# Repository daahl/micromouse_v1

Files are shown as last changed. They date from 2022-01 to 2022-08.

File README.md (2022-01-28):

# Micromouse_v1

This project aims to develop a [micromouse](https://www.youtube.com/results?search_query=micromouse) using a DOIT ESP32 dev module. The robot is powered by two 18620 batteries in series, and two micro metal motors fitted with encoders. The mapping is done using three VL53L0X TOF sensors.

**Currently a work in progress.**

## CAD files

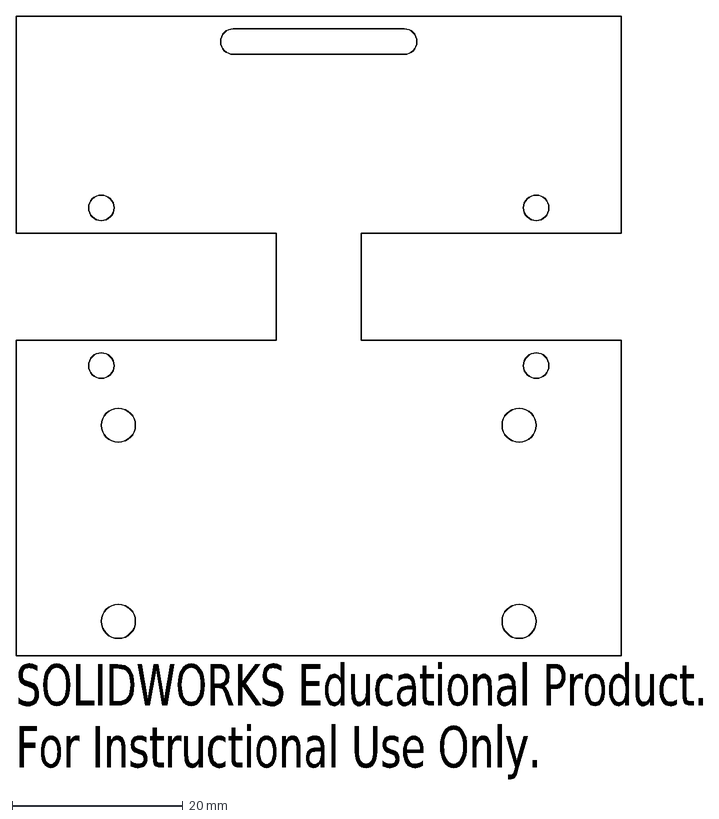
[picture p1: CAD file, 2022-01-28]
kicad_v2/PCB.dxf
SOLIDWORKS Educational Product.
For Instructional Use Only.

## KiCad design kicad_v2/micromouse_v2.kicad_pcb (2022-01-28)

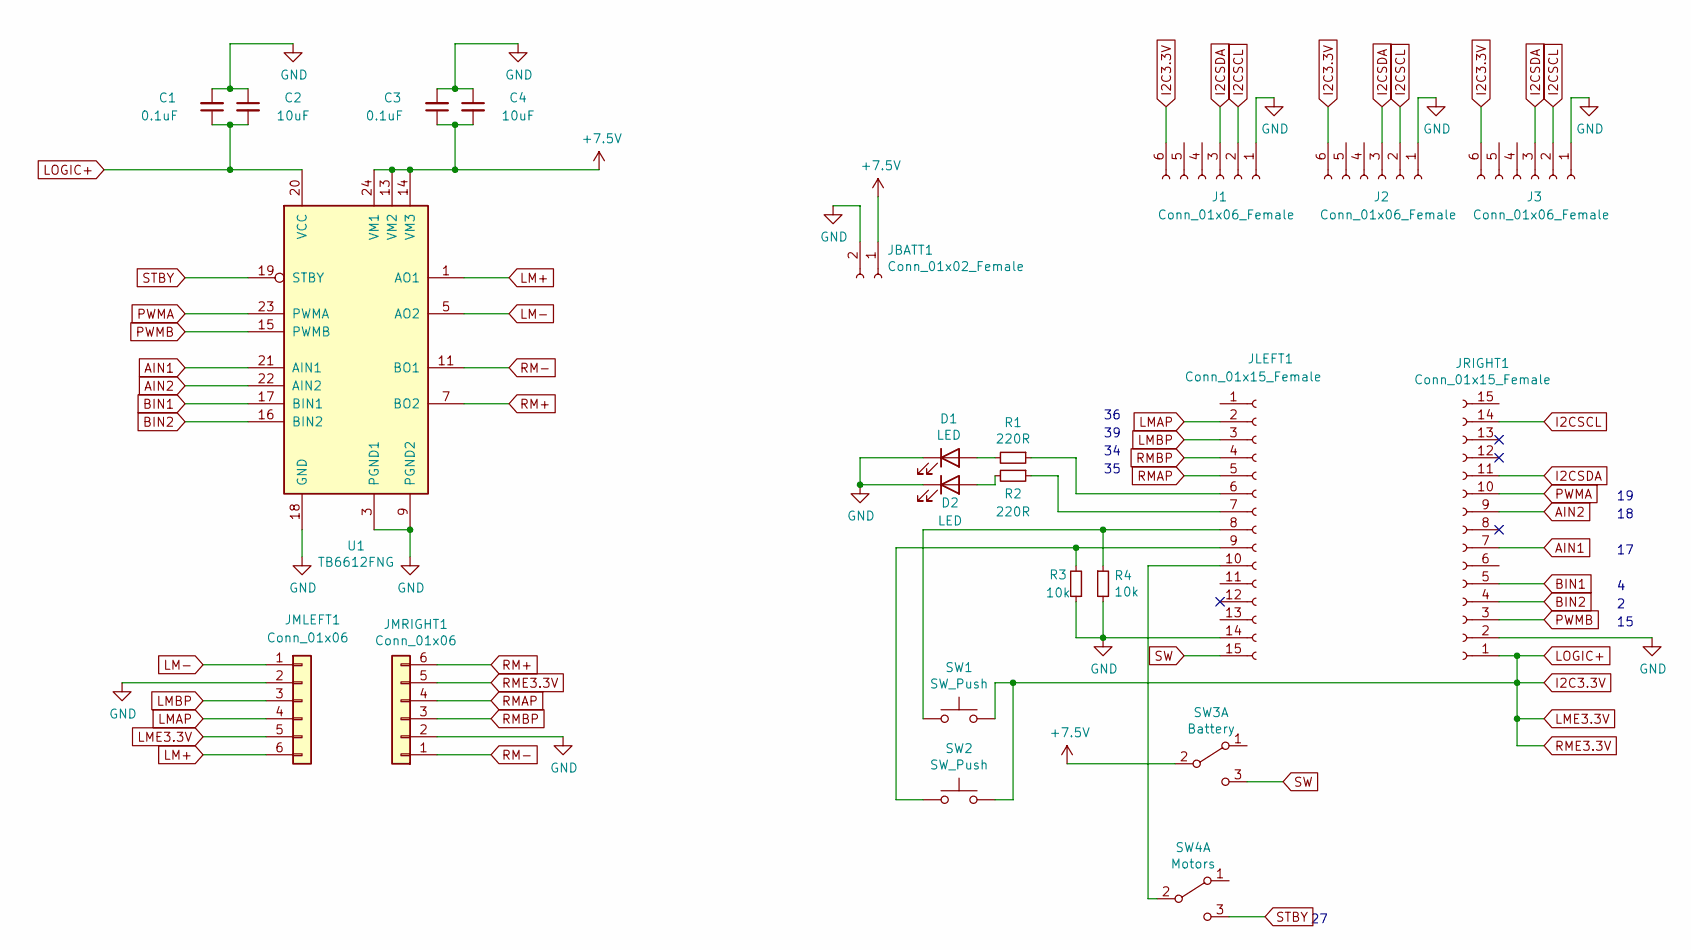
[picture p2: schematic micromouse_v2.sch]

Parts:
C1, C3: 0.1uF; C_0603_1608Metric_Pad1.08x0.95mm_HandSolder
C2, C4: 10uF; C_0603_1608Metric_Pad1.08x0.95mm_HandSolder
D1, D2: LED; LED_0603_1608Metric_Pad1.05x0.95mm_HandSolder
J1, J2, J3: Conn_01x06_Female; PinSocket_1x06_P2.54mm_Vertical
JBATT1: Conn_01x02_Female; JST_EH_B2B-EH-A_1x02_P2.50mm_Vertical
JLEFT1: Conn_01x15_Female; PinSocket_1x15_P2.54mm_Vertical
JMLEFT1: Conn_01x06; JST_EH_B6B-EH-A_1x06_P2.50mm_Vertical
JMRIGHT1: Conn_01x06; JST_EH_B6B-EH-A_1x06_P2.50mm_Vertical
JRIGHT1: Conn_01x15_Female; PinSocket_1x15_P2.54mm_Vertical
R1, R2: 220R; R_0603_1608Metric_Pad0.98x0.95mm_HandSolder
R3, R4: 10k; R_0603_1608Metric_Pad0.98x0.95mm_HandSolder
SW1, SW2: SW_Push; SW_SPST_Omron_B3FS-100xP
SW3: Battery; SW_CuK_OS102011MA1QN1_SPDT_Angled
SW4: Motors; SW_CuK_OS102011MA1QN1_SPDT_Angled
U1: TB6612FNG; SSOP-24_5.3x8.2mm_P0.65mm

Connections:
+7.5V: C3.1, C4.2, JBATT1.1, SW3.2 (B), U1.13 (VM2), U1.14 (VM3), U1.24 (VM1)
AIN1: JRIGHT1.7, U1.21 (AIN1)
AIN2: JRIGHT1.9, U1.22 (AIN2)
BIN1: JRIGHT1.5, U1.17 (BIN1)
BIN2: JRIGHT1.4, U1.16 (BIN2)
GND: C1.2, C2.1, C3.2, C4.1, D1.1 (K), D2.1 (K), J1.1, J2.1, J3.1, JBATT1.2, JLEFT1.14, JMLEFT1.2, JMRIGHT1.2, JRIGHT1.2, R3.1, R4.2, U1.3 (PGND1), U1.4 (PGND1), U1.9 (PGND2), U1.10 (PGND2), U1.18 (GND)
I2C3.3V: C1.1, C2.2, J1.6, J2.6, J3.6, JMLEFT1.5, JMRIGHT1.5, JRIGHT1.1, SW1.2, SW2.2, U1.20 (VCC)
I2CSCL: J1.2, J2.2, J3.2, JRIGHT1.14
I2CSDA: J1.3, J2.3, J3.3, JRIGHT1.11
LM+: JMLEFT1.6, U1.1 (AO1), U1.2 (AO1)
LM-: JMLEFT1.1, U1.5 (AO2), U1.6 (AO2)
LMAP: JLEFT1.2, JMLEFT1.4
LMBP: JLEFT1.3, JMLEFT1.3
unnamed: D1.2 (A), R1.2
unnamed: D2.2 (A), R2.2
unnamed: JLEFT1.6, R1.1
unnamed: JLEFT1.7, R2.1
unnamed: JLEFT1.8, R4.1, SW1.1
unnamed: JLEFT1.9, R3.2, SW2.1
unnamed: JLEFT1.10, SW4.2 (B)
PWMA: JRIGHT1.10, U1.23 (PWMA)
PWMB: JRIGHT1.3, U1.15 (PWMB)
RM+: JMRIGHT1.6, U1.7 (BO2), U1.8 (BO2)
RM-: JMRIGHT1.1, U1.11 (BO1), U1.12 (BO1)
RMAP: JLEFT1.5, JMRIGHT1.4
RMBP: JLEFT1.4, JMRIGHT1.3
STBY: SW4.3 (C), U1.19 (STBY)
SW: JLEFT1.15, SW3.3 (C)

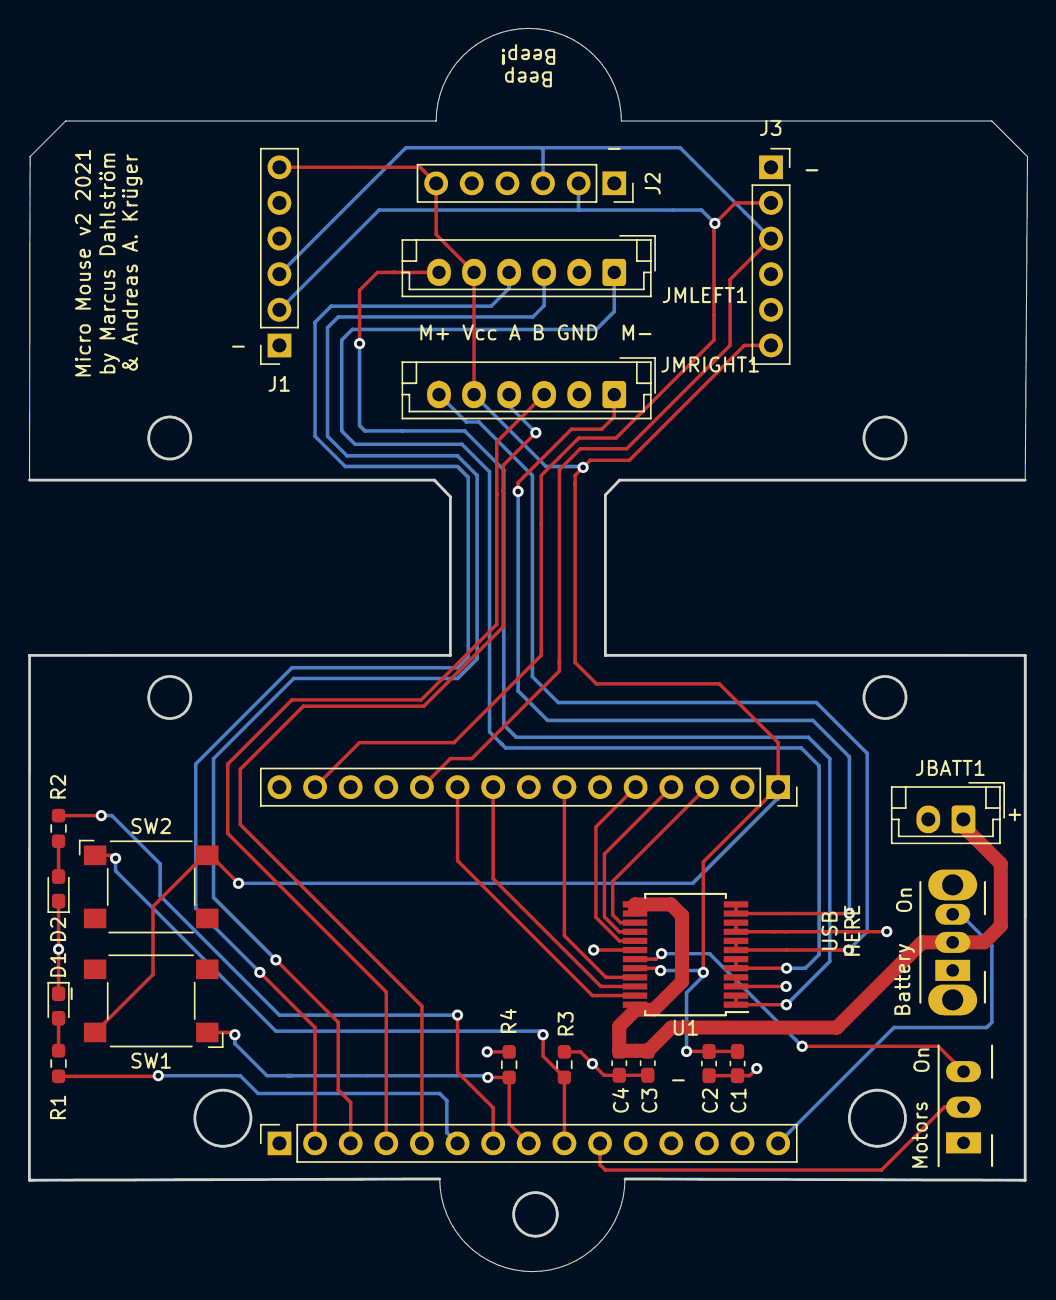
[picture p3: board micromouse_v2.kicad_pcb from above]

Board: 2 copper layers, 71.2 x 88.6 mm, 23 parts (0 on the bottom side), 28 nets.

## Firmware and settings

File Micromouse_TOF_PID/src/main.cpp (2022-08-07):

/*
#include <Arduino.h>
#include <Wire.h>
#include "Adafruit_VL53L0X.h" // TOF library
#include "SparkFun_TB6612.h"  // Motor driver library

//########## General setup ##########
#define LED1 32
#define LED2 33

//########## TOF sensor setup ##########
// define TOF sensor addresses
#define LOXLL_ADDR 0x2A // left
#define LOXCC_ADDR 0x2B // center
#define LOXRR_ADDR 0x2C // right

// sensor objects
Adafruit_VL53L0X loxLL = Adafruit_VL53L0X();
Adafruit_VL53L0X loxCC = Adafruit_VL53L0X();
Adafruit_VL53L0X loxRR = Adafruit_VL53L0X();

//########## Motor setup ##########
// Motor driver
#define AIN1    17
#define AIN2    18
#define PWMA    19
#define LOFFSET -1
#define BIN1    4
#define BIN2    2
#define PWMB    15
#define ROFFSET -1
#define STBY    27

// Motor encoders
#define encoderLLAA  36
#define encoderLLBB  39
#define encoderRRAA  35
#define encoderRRBB  34

// Motor objects to control the motors
Motor motorLL = Motor(AIN1, AIN2, PWMA, LOFFSET, STBY);
Motor motorRR = Motor(BIN1, BIN2, PWMB, ROFFSET, STBY);

// Motor positions
int posLL = 0;
int posRR = 0;

//########## PID setup ##########
// PID variables
int prevT = 0;
float errprev = 0.0;
float errintegral = 0.0;
float speedLL = 0;
float speedRR = 0;

// define PID parameters
float kp = 3;
float kd = 0.05;
float ki = 0.0;

//
// Scans the i2c address domain and prints the found sensors
//
void Scanner ()
{
  Serial.println ();
  Serial.println ("I2C scanner. Scanning ...");
  byte count = 0;

  for (byte i = 8; i < 120; i++)
  {
    Wire.beginTransmission (i);          // Begin I2C transmission Address (i)
    if (Wire.endTransmission () == 0)  // Receive 0 = success (ACK response) 
    {
      Serial.print ("Found address: ");
      Serial.print (i, DEC);
      Serial.print (" (0x");
      Serial.print (i, HEX);     // PCF8574 7 bit address
      Serial.println (")");
      count++;
    }
  }
  Serial.print ("Found ");      
  Serial.print (count, DEC);        // numbers of devices
  Serial.println (" device(s).");
}

//
// Reads the left motor encoder and tracks its rotations
//
void readEncoderLL(){
  int b = digitalRead(encoderLLBB);
  // Add to pos on clockwise rotation
  if(b > 0){
    posLL--;
  }
  else{
    posLL++;
  }
}


//
// Reads the right motor encoder and tracks its rotations
//
void readEncoderRR(){
  int b = digitalRead(encoderRRBB);
  // Add to pos on counter clockwise rotation
  if(b > 0){
    posRR++;
  }
  else{
    posRR--;
  }
}

void setup() {
  //########## General setup ##########
  Serial.begin(9600);
  pinMode(LED1, OUTPUT);
  pinMode(LED2, OUTPUT);

  //########## TOF sensor setup ##########
  // notice! you have to plug them in one-by-one when the setup is running...
  // thanks for making the address non-writable ST
  Wire.begin();

  // start with the left sensor
  Serial.println("Setup starting for LEFT sensor...");
  delay(5000);
  // wait for the left sensor to respond
  while(1){
    Serial.println("Waiting for sensor to respond...");
    digitalWrite(LED1, HIGH);
    loxLL.begin(); // default address is 0x29 for all lox sensors
    loxLL.setAddress(LOXLL_ADDR);
    Wire.beginTransmission(LOXLL_ADDR);
    if(Wire.endTransmission() == 0){ // Receive 0 = success
      break;
    }
    delay(500);
  }
  Serial.println("LEFT sensor setup successfully!");
  Serial.println("Please insert CENTER sensor within 5 seconds...");
  delay(7000);

  // then the CENTER sensor
  // wait for the center sensor to respond
  while(1){
    Serial.println("Waiting for sensor to respond...");
    digitalWrite(LED1, HIGH);
    digitalWrite(LED2, HIGH);
    loxCC.begin(); // default address is 0x29 for all lox sensors
    loxCC.setAddress(LOXCC_ADDR);
    Wire.beginTransmission(LOXCC_ADDR);
    if(Wire.endTransmission() == 0){ // Receive 0 = success
      break;
    }
    delay(500);
  }
  Serial.println("CENTER sensor setup successfully!");
  Serial.println("Please insert RIGHT sensor within 5 seconds...");
  delay(7000);

  // finally the right sensor
  // wait for the left sensor to respond
  while(1){
    Serial.println("Waiting for sensor to respond...");
    digitalWrite(LED1, LOW);
    digitalWrite(LED2, HIGH);
    loxRR.begin(); // default address is 0x29 for all lox sensors
    loxRR.setAddress(LOXRR_ADDR);
    Wire.beginTransmission(LOXRR_ADDR);
    if(Wire.endTransmission() == 0){ // Receive 0 = success
      break;
    }
    delay(500);
  }
  Serial.println("RIGHT sensor setup successfully!");
  Serial.println("Setup complete for ALL sensors!");
  digitalWrite(LED1, HIGH);
  digitalWrite(LED2, HIGH);
  delay(250);
  digitalWrite(LED1, LOW);
  digitalWrite(LED2, LOW);
  delay(250);
  digitalWrite(LED1, HIGH);
  digitalWrite(LED2, HIGH);
  delay(250);
  digitalWrite(LED1, LOW);
  digitalWrite(LED2, LOW);
  delay(250);
  Scanner();
  //########## Motor setup ##########
  // Left motor encoder
  pinMode(encoderLLAA, INPUT);
  pinMode(encoderLLBB, INPUT);
  attachInterrupt(digitalPinToInterrupt(encoderLLAA), readEncoderLL, RISING);
  // Right motor encoder
  pinMode(encoderRRAA, INPUT);
  pinMode(encoderRRBB, INPUT);
  attachInterrupt(digitalPinToInterrupt(encoderRRAA), readEncoderRR, RISING);
  Serial.println("Motor setup complete!");

  delay(2000);
}


void loop() {
  //########## Read the TOF sensors ##########
  // range measurement variables
  VL53L0X_RangingMeasurementData_t measureLL;
  VL53L0X_RangingMeasurementData_t measureCC;
  VL53L0X_RangingMeasurementData_t measureRR;

  
  loxLL.rangingTest(&measureLL, false);
  loxCC.rangingTest(&measureCC, false);
  loxRR.rangingTest(&measureRR, false);

  int distLL = measureLL.RangeMilliMeter;
  int distCC = measureCC.RangeMilliMeter;
  int distRR = measureRR.RangeMilliMeter;

  if(measureLL.RangeStatus != 4 && measureCC.RangeStatus != 4 && measureRR.RangeStatus != 4){
    Serial.print("Distance (mm): "); 
    Serial.print(distLL);
    Serial.print(" ");
    Serial.print(distCC);
    Serial.print(" ");
    Serial.println(distRR);
  }
  else{
    Serial.println("One sensor is out of range...");
  }
  
  //########## Do some PID stuff ##########
  // time difference
  float currT = micros();
  float deltaT = ((float)(currT - prevT)/1.0e6);
  prevT = currT;

  // current error
  int err = distLL - distRR; // negative = too far right, positive = too far left

  // derivative
  float dedt = (err - errprev)/deltaT;

  // integral
  errintegral = errintegral + err*deltaT;

  // control signal
  float u = kp*err + kd*dedt + ki*errintegral;


  // motor power
  if(err < 0){ // drive further left
    speedLL = fabs(u);
    speedRR = 0;
  }
  else if(err > 0){ // drive further right
    speedLL = 0;
    speedRR = fabs(u);
  }
  else{
    speedLL = 0;
    speedRR = 0;
  }

  // Limit the extra speed that error corection gives
  if(speedLL > 100){
    speedLL = 100;
  }
  if(speedRR > 100){
    speedRR = 100;
  }

  // store previous error
  errprev = err;

  // signal the motors
  motorLL.drive(speedLL + 50);
  motorRR.drive(speedRR + 50);

  Serial.println(err);
  Serial.println();
}*/
// Code above was the old one. Code below is with Blynk.app
/*************************************************************

  This is a simple demo of sending and receiving some data.
  Be sure to check out other examples!
 *************************************************************/

// Template ID, Device Name and Auth Token are provided by the Blynk.Cloud
// See the Device Info tab, or Template settings
#define BLYNK_TEMPLATE_ID           "TMPLONAKqwBH"
#define BLYNK_DEVICE_NAME           "Quickstart Device"
#define BLYNK_AUTH_TOKEN            "H0kLMv5MtTSdw-0jVQvkUl56ezXpYRFl"


// Comment this out to disable prints and save space
#define BLYNK_PRINT Serial


#include <WiFi.h>
#include <WiFiClient.h>
#include <BlynkSimpleEsp32.h>

char auth[] = BLYNK_AUTH_TOKEN;

// Your WiFi credentials.
// Set password to "" for open networks.
char ssid[] = "Mulldalen";
char pass[] = "vilseiskogen";

BlynkTimer timer;

// This function is called every time the Virtual Pin 0 state changes
BLYNK_WRITE(V0)
{
  // Set incoming value from pin V0 to a variable
  int value = param.asInt();

  // Update state
  Blynk.virtualWrite(V1, value);
}

// This function is called every time the device is connected to the Blynk.Cloud
BLYNK_CONNECTED()
{
  // Change Web Link Button message to "Congratulations!"
  Blynk.setProperty(V3, "offImageUrl", "https://static-image.nyc3.cdn.digitaloceanspaces.com/general/fte/congratulations.png");
  Blynk.setProperty(V3, "onImageUrl",  "https://static-image.nyc3.cdn.digitaloceanspaces.com/general/fte/congratulations_pressed.png");
  Blynk.setProperty(V3, "url", "https://docs.blynk.io/en/getting-started/what-do-i-need-to-blynk/how-quickstart-device-was-made");
}

// This function sends Arduino's uptime every second to Virtual Pin 2.
void myTimerEvent()
{
  // You can send any value at any time.
  // Please don't send more that 10 values per second.
  Blynk.virtualWrite(V2, millis() / 1000);
}

void setup()
{
  // Debug console
  Serial.begin(115200);

  Blynk.begin(auth, ssid, pass);
  // You can also specify server:
  //Blynk.begin(auth, ssid, pass, "blynk.cloud", 80);
  //Blynk.begin(auth, ssid, pass, IPAddress(192,168,1,100), 8080);

  // Setup a function to be called every second
  timer.setInterval(1000L, myTimerEvent);
}

void loop()
{
  Blynk.run();
  timer.run();
  // You can inject your own code or combine it with other sketches.
  // Check other examples on how to communicate with Blynk. Remember
  // to avoid delay() function!
}

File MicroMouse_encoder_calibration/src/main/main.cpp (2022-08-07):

/*#include <Arduino.h>
#include "SparkFun_TB6612.h"

// Motor driver
#define AIN1    17
#define AIN2    18
#define PWMA    19
#define LOFFSET -1
#define BIN1    4
#define BIN2    2
#define PWMB    15
#define ROFFSET -1
#define STBY    27

// Motor encoders
#define encoderLLAA  36
#define encoderLLBB  39
#define encoderRRAA  35
#define encoderRRBB  34

// Motor objects to control the motors
Motor motorLL = Motor(AIN1, AIN2, PWMA, LOFFSET, STBY);
Motor motorRR = Motor(BIN1, BIN2, PWMB, ROFFSET, STBY);

// "Absolute" motor positions are set to 0 on startup
int absPosLL = 0;
int absPosRR = 0;

// acceleration parameters
float accLL = 0.0;
float accRR = 0.0;
float accLim = 0.75;
float deaccLim = 0.40;
float speedLim = 0.0;
float accSpeed = 3.0;
float deaccSpeed = 30.0;
int whineLim = 15;

// state varaibles
bool parked = 1;
bool accelerating = 0;
bool driving = 0;
bool deaccelerating = 0;
float distanceLim = 3.0;

// PID variables
int prevT = 0;
float eprevLL = 0.0;
float eprevRR = 0.0;
float eintegralLL = 0.0;
float eintegralRR = 0.0;
float speedLL = 0.0;
float speedRR = 0.0;

// define PID parameters
float kp = 7; //7
float kd = 0.1; //0.1
float ki = 0.0; //0

void readEncoderLL(){
  int b = digitalRead(encoderLLBB);
  // Add to pos on clockwise rotation
  if(b > 0){
    absPosLL--;
  }
  else{
    absPosLL++;
  }
}

void readEncoderRR(){
  int b = digitalRead(encoderRRBB);
  // Add to pos on counter clockwise rotation
  if(b > 0){
    absPosRR++;
  }
  else{
    absPosRR--;
  }
}

//
//  Return the absolute distance to the target.
//  0 = left motor
//  1 = right motor
//
float absDist2Target(int target, bool leftOrRight){
  if(leftOrRight)
  {
    return fabs(target - absPosRR);
  }else{
    return fabs(target - absPosLL);
  }
  
}

//
//  Regulates the speed to the motors. Has to be constantly called to regulate.
//
void PID(int targetLL, int targetRR){
  // time difference
  float currT = micros();
  float deltaT = ((float)(currT - prevT)/1.0e6);
  prevT = currT;

  // current error
  int eLL = targetLL - absPosLL;
  int eRR = targetRR - absPosRR;

  // derivative
  float dedtLL = (eLL - eprevLL)/deltaT;
  float dedtRR = (eRR - eprevRR)/deltaT;

  // integral
  eintegralLL = eintegralLL + eLL*deltaT;
  eintegralRR = eintegralRR + eRR*deltaT;

  // control signal
  float uLL = kp*eLL + kd*dedtLL + ki*eintegralLL;
  float uRR = kp*eRR + kd*dedtRR + ki*eintegralRR;

  // set and limit motor power
  speedLL = fabs(uLL);
  
  if(speedLL > speedLim){
    speedLL = speedLim;
  }
  speedRR = fabs(uRR);
  if(speedRR > speedLim){
    speedRR = speedLim;
  }

  // motor directions
  int dirLL = 1;
  if(uLL < 0){
    dirLL = -1;
  }
  int dirRR = 1;
  if(uRR < 0){
    dirRR = -1;
  }
  
  // store previous error
  eprevLL = eLL;
  eprevRR = eRR;

  // signal the motor
  motorLL.drive(dirLL*(int)speedLL);
  motorRR.drive(dirRR*(int)speedRR);

  // debug prints
  Serial.print("posLL:");
  Serial.print(absPosLL);
  Serial.print(",");
  Serial.print("posRR:");
  Serial.print(absPosRR);
  Serial.print(",");
  Serial.print("targetLL:");
  Serial.print(targetLL);
  Serial.print(",");
  Serial.print("targetRR:");
  Serial.println(targetRR);
}

//
//  State handling function to give the micromouse acceleration and deacceleration
//
void driveTo(int distanceLL, int distanceRR){
  float targetLL = absPosLL + distanceLL;
  float targetRR = absPosRR + distanceRR;

  // ### Parked state ### //
  while(parked){
    // too far away from target, change from parked to accelerating
    if(absDist2Target(targetLL, 0) > distanceLim or absDist2Target(targetRR, 1) > distanceLim){
    parked = 0;
    accelerating = 1;
    Serial.println("##### Accelerating #####");
    }
  }

  // ### Accelerating state ### //
  while(accelerating){
    if(speedLim < 255){
      speedLim += accSpeed;
    }
    PID(targetLL, targetRR);

    // accelerate until accLim% distance remains
    if((absDist2Target(targetLL, 0) <= accLim*fabs(distanceLL)) and (absDist2Target(targetRR, 1) <= accLim*fabs(distanceRR))){
      accelerating = 0;
      driving = 1;
      Serial.println("##### Driving #####");

      // short disances causes the speedLim to be too low,
      // minimum speed to move forward is 50.
      if(speedLim < 50){
        speedLim = 50;
      }
    }
  }

  // ### Driving state ### //
  while(driving){
    PID(targetLL, targetRR);

    // begin deaccelerating when deaccLim% distance remains
    if((absDist2Target(targetLL, 0) <= deaccLim*fabs(distanceLL)) and (absDist2Target(targetRR, 1) <= deaccLim*fabs(distanceRR))){
      driving = 0;
      deaccelerating = 1;
      Serial.println("##### Deaccelerating #####");
    }
  }

  // ### Deaccelerating state ### //
  while(deaccelerating){
    if(speedLim >= 70){
      speedLim -= deaccSpeed;
    }
    PID(targetLL, targetRR);

    // stop deaccelerating when close enough to target
    if(absDist2Target(targetLL, 0) <= distanceLim and absDist2Target(targetRR, 1) <= distanceLim){
      deaccelerating = 0;
      parked = 1;
      speedLim = 0.0;
      motorLL.brake();
      motorRR.brake();
      Serial.println("##### Parked #####");
    }
  }
}

void setup() {
  Serial.begin(115200);
  // Left motor encoder
  pinMode(encoderLLAA, INPUT);
  pinMode(encoderLLBB, INPUT);
  attachInterrupt(digitalPinToInterrupt(encoderLLAA), readEncoderLL, RISING);

  // Right motor encoder
  pinMode(encoderRRAA, INPUT);
  pinMode(encoderRRBB, INPUT);
  attachInterrupt(digitalPinToInterrupt(encoderRRAA), readEncoderRR, RISING);
  delay(4000);
}

void loop(){
    driveTo(500, 500);
    delay(700);
    driveTo(-345, +345);
    delay(700);
}*/
/*************************************************************

  This is a simple demo of sending and receiving some data.
  Be sure to check out other examples!
 *************************************************************/
//#include <Arduino.h>
#include <WiFi.h>
#include <WiFiClient.h>
#include <BlynkSimpleEsp32.h>
//#include "SparkFun_TB6612.h"

// Template ID, Device Name and Auth Token are provided by the Blynk.Cloud
// See the Device Info tab, or Template settings
#define BLYNK_TEMPLATE_ID "TMPLzIux-iXu"
#define BLYNK_DEVICE_NAME "Micromouse v2"
#define BLYNK_AUTH_TOKEN "2FeJeGJ-Ofr3sv2tWK5VPHD_gEaWwQE8"

// Comment this out to disable prints and save space
#define BLYNK_PRINT Serial

// Hardware pins
#define BOARD_LED_1 32

// Motor driver
#define AIN1    17
#define AIN2    18
#define PWMA    19
#define LOFFSET -1
#define BIN1    4
#define BIN2    2
#define PWMB    15
#define ROFFSET -1
#define STBY    27

// Motor objects and variables to control the motors
//Motor motorLL = Motor(AIN1, AIN2, PWMA, LOFFSET, STBY);
//Motor motorRR = Motor(BIN1, BIN2, PWMB, ROFFSET, STBY);
int speed = 0;
int turn = 0;

char auth[] = BLYNK_AUTH_TOKEN;

// Your WiFi credentials.
// Set password to "" for open networks.
char ssid[] = "Mulldalen";
char pass[] = "vilseiskogen";

BlynkTimer timer;
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

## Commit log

2022-08-07 Drive given distance fixed
    [main.cpp]
2022-08-07 Motor functions but errors
    [main.cpp]
